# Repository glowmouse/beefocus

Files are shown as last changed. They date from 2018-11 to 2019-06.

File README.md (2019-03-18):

Beefocus
========

Beefocus is an Open Source Hardware/ Software Telescope Focuser 
The goal of the project is to create a high quality DIY focuser that's
relatively easy to build and modify.

It's similar in spirit to other open source focuser projects.  For
example...

- https://sourceforge.net/projects/arduinoascomfocuserpro2diy/
- http://www.scopefocus.info/arduino-focuser-2
- https://sourceforge.net/projects/arduinomoonlitefocuserclone/?source=directory
- https://github.com/aruangra/PnP-Focus

Why start a new project?
------------------------

- **Originally, I needed a custom focuser solution for my telescope**.
  I have a Celestron C11 with a Hyperstar.  When I started this I
  couldn't find a good out of the box solution.
- **I want to try using an ESP-8266 internet of things micro-controller 
  instead of a traditional arduino**.  I've found that every wire you 
  get rid of simplifies your telescope setup and observing
- **I want to open-source the hardware design under a permissive license.**   
  I'm intrigued by the idea of open-source hardware.  I'm including the
  Eagle CAD files for the hardware under a Creative Commons 4.0 license.
  The goal is to make builds as inexpensive and easy as possible.
- This project is a good personal learning experience.

Code Documentation
------------------

Documentation can be found at https://glowmouse.github.io/beefocus/ 

Status March 2019
-----------------

- I have a physical prototype. It's been field tested and
  it worked almost flawlessly.  The issues that I want to fix before
  "Version 1.0" are tracked on the [Github Project Issues Page].
- The [Prototype ESP8266 Firmware] is posted.  The only thing I want to
  fix in the Firmware is the way you hook up to the Wifi Network.
  Right now you have to modify the Firmware Source Code to add your
  SSID and Password.
- I've published a [Prototype Board Design].  I made my prototype using 
  a CNC circuit router. I had an initial version of the board professionally
  fabricated, and it had a flaw :(.  I'll make a new version of the board
  when I make setting the SSID and Password more user friendly.  I'm also
  waiting for some parts from Ebay.
- There is an INDI Driver for Beefocus, the driver is in the
  [INDI Github Repository] in the [3rd Party Beefocus] directory.
- I've created a [Beefocus INDI Usage] page.

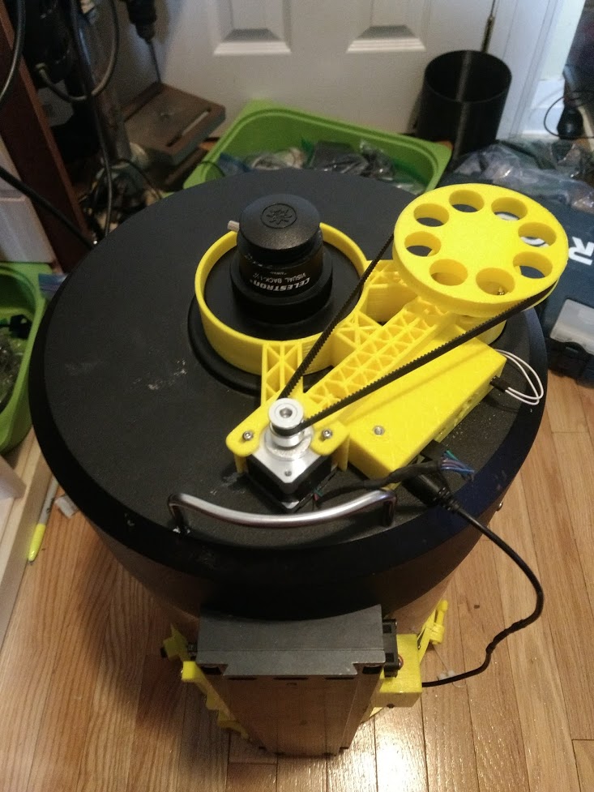
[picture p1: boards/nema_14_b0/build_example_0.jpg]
Nema 14 Build Example


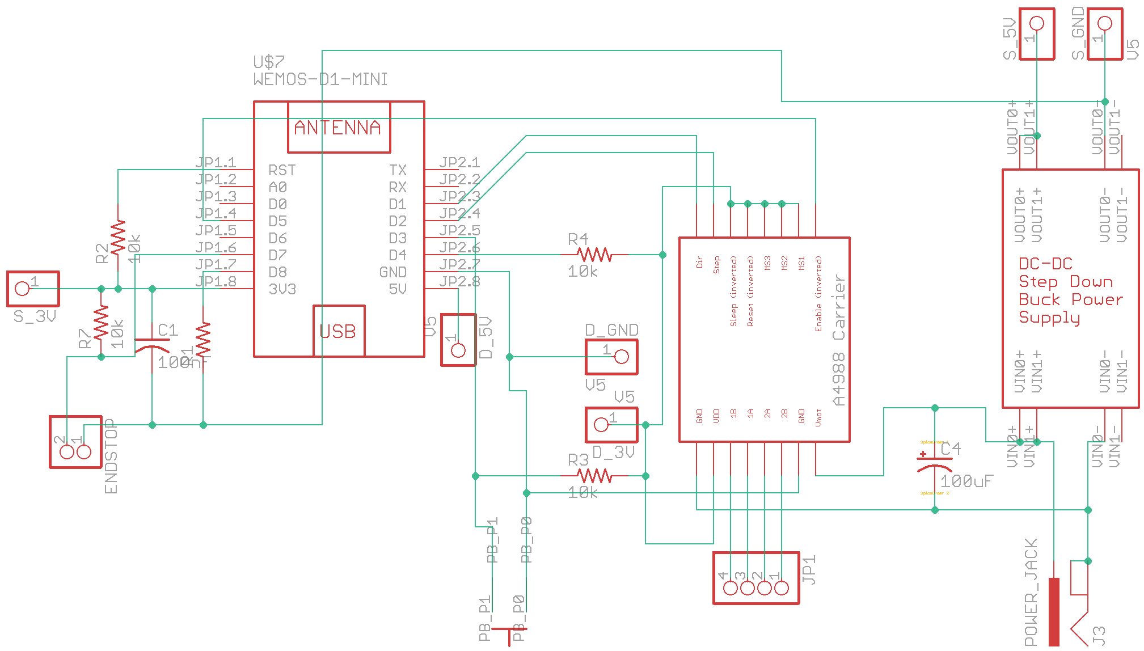
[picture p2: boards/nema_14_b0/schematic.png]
Nema 14 Build Schematic


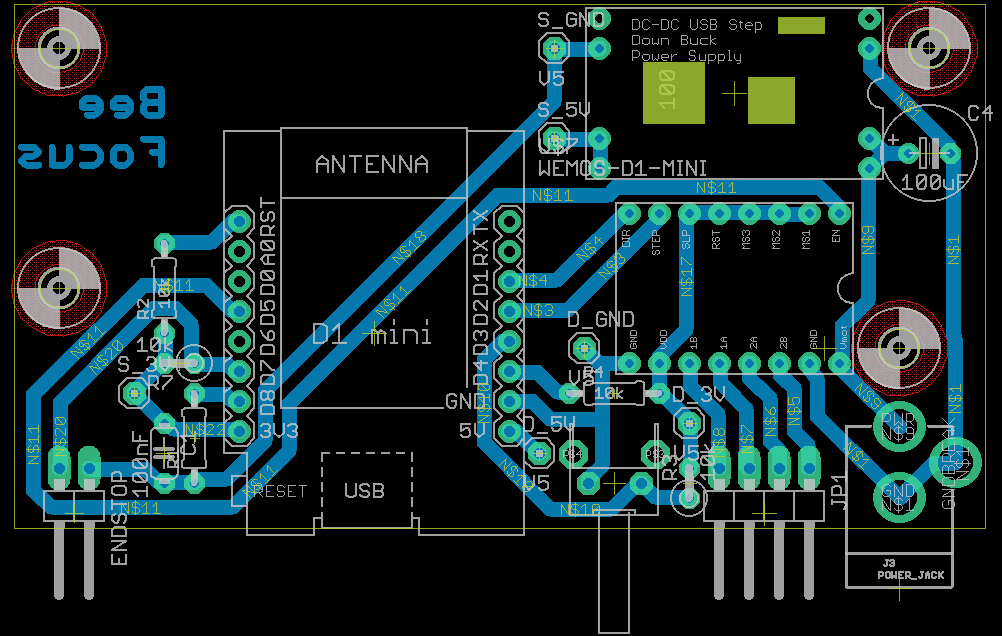
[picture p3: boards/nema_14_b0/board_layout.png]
Nema 14 Build Board


[Github Project Issues Page]:https://github.com/glowmouse/beefocus/issues
[Prototype ESP8266 firmware]: https://github.com/glowmouse/beefocus/tree/master/firmware
[INDI Github Repository]: https://github.com/indilib/indi
[3rd Party Beefocus]: https://github.com/indilib/indi/tree/master/3rdparty/indi-beefocus 
[Prototype board design]: https://github.com/glowmouse/beefocus/tree/master/boards/nema_14_b0
[Beefocus INDI Usage]: https://github.com/glowmouse/beefocus/blob/master/indi_docs/indi_usage_docs.md

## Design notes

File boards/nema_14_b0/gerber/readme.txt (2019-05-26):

Tested gerber files for the nema_14_b0 board.  The board worked, but the DC to DC converters I used in this board aren't sold anymore.  I've moved on to nema_14_b1.

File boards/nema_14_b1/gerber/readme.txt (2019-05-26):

Untested gerber files for the nema_14_b1 board.  I've sent the board out
to get it made, but there are no guarantees that these files will work.

Status:  May 26 2019,  waiting to receive boards.

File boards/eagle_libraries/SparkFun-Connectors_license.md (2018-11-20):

SparkFun Connectors

Licensing: Creative Commons ShareAlike 4.0 International - https://creativecommons.org/licenses/by-sa/4.0/ 

Original source and attriubutio: https://github.com/sparkfun/SparkFun-Eagle-Libraries

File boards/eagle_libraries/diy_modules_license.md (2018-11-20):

DIY Modules Library for EAGLE PCB Design Software has been released under the Creative Commons Attribution 4.0 International License: http://creativecommons.org/licenses/by/4.0.

The library was originally sourced from https://www.diymodules.org/eagle.  The version used by this project is 1.8.0

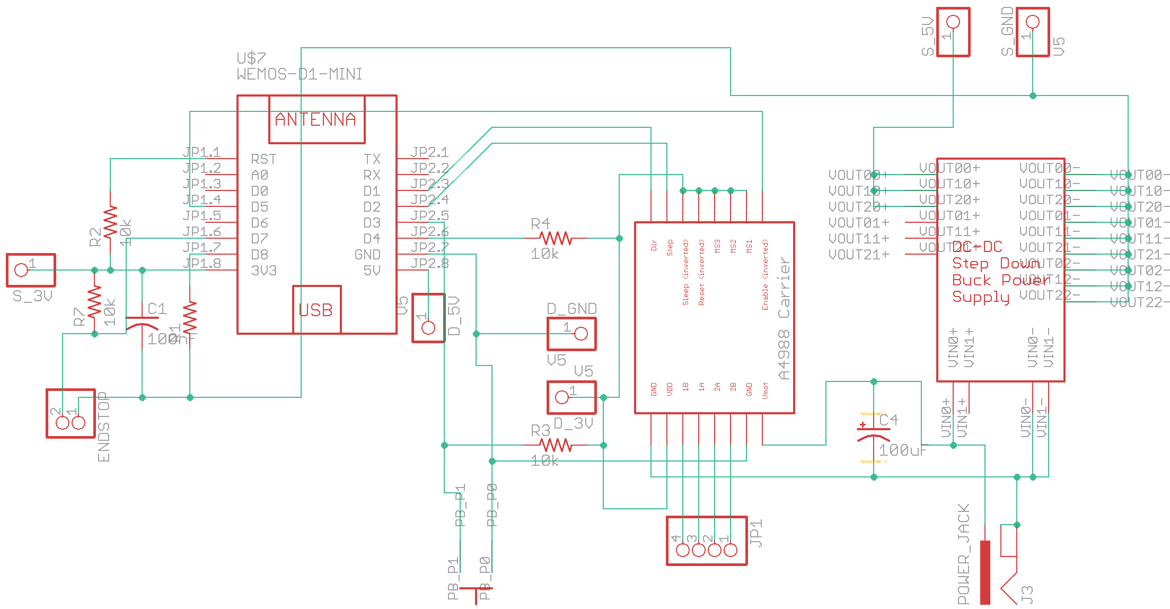
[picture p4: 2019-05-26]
boards/nema_14_b1/schematic.png

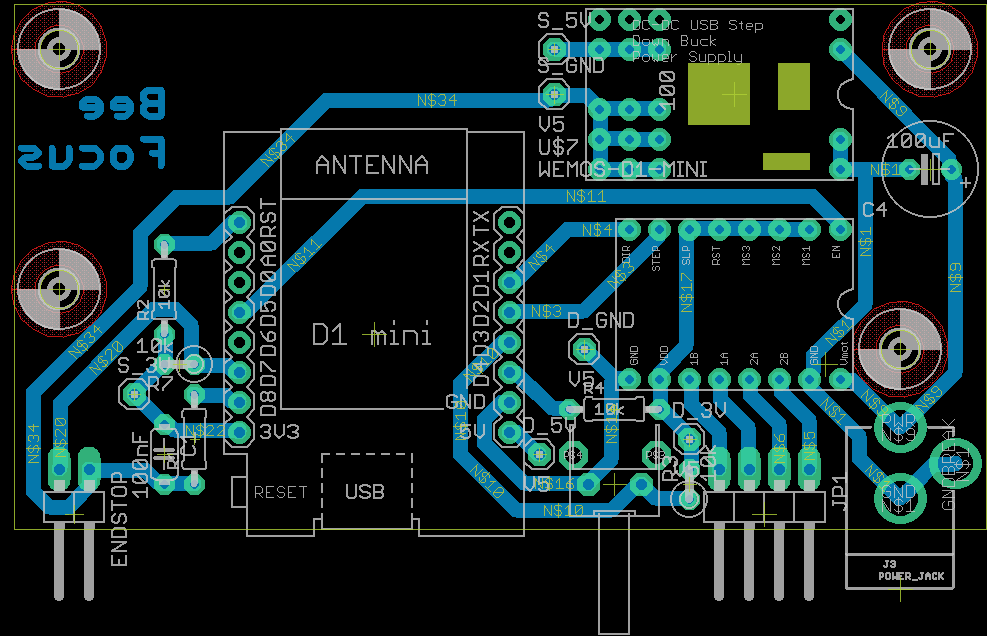
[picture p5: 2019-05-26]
boards/nema_14_b1/board_layout.png

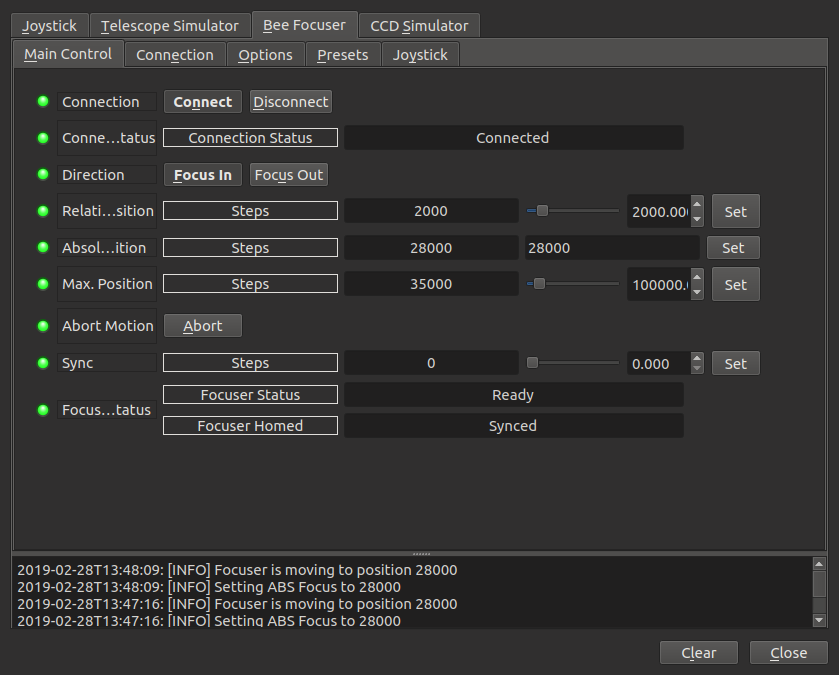
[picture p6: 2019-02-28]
indi_docs/con_sim_abs_dst_ready.png

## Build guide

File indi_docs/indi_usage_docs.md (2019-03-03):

Beefocused
==========

Beefocused is an Open Source Hardware/ Software Telescope Focuser
The goal of the project is to create a high quality DIY focuser that's
relatively easy to build and modify.

Installation
------------

- Beefocused can only be built from source right now (and only on Indi -
  https://indilib.org/ ) - ASCOM drivers haven't been written yet.  
  If you're interested in building one send an email to 
  andrew.brownbill@gmail.com

Features
--------

- Beefocused talks to the INDI computer using WiFi.  This is nice because
  it means there's one less wire on the telescope to worry about.  It does 
  mean that the telescope needs a WiFi hotspot,  but that's becoming more 
  common now that people are running telescopes from compute sticks and 
  Raspberry Pis that are mounted directly onto the scope.
- The default built uses a Nema 14 Stepper motor for positioning - these motors
  are widely used by 3D printers.  The Motor's step rate is 1.8 degrees 
  (200 steps / rotation), so it's reasonably accurate.
- The electronic parts for a Beefocused will cost you about $25 on eBay.
  That includes the Nema 14 Stepper Motor. 
- Beefocus focusers operate as either Absolute or Relative focusers,
  depending on the build.  The focuser supports either automatic homing at
  start up or manual syncing.

Using the Simulated Focuser
---------------------------

The Beefocused Indi driver has a "Simulation" mode that's very close to what
you'll see if you use the actual hardware.  Simulation mode is selected by
going to the BeeFocused connection tab and selecting a Simulated connection

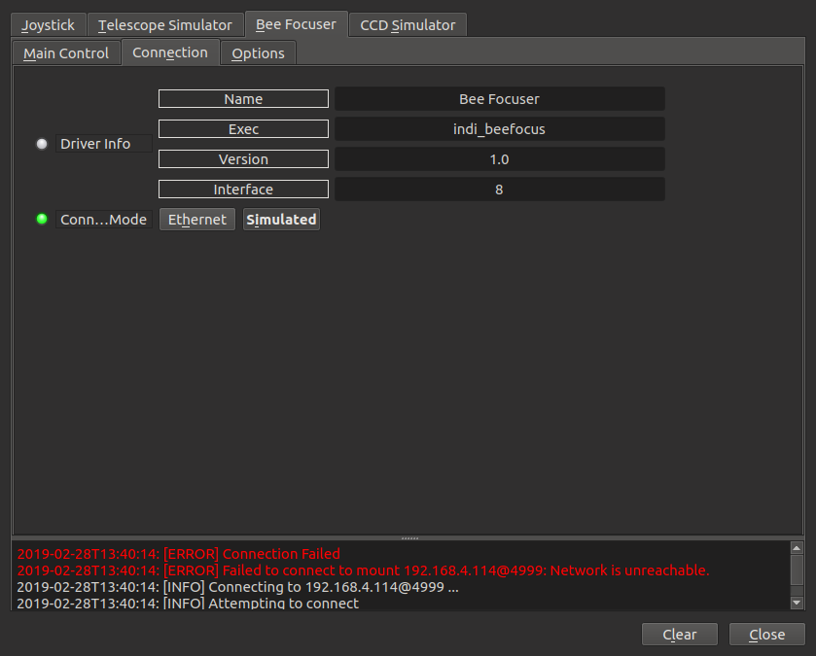
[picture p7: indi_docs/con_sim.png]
Selecting a Simulated Connection


You'll need to go to the Main focuser menu and "connect" to the Simulated
Focuser, the way you'd connect to an actual focuser.

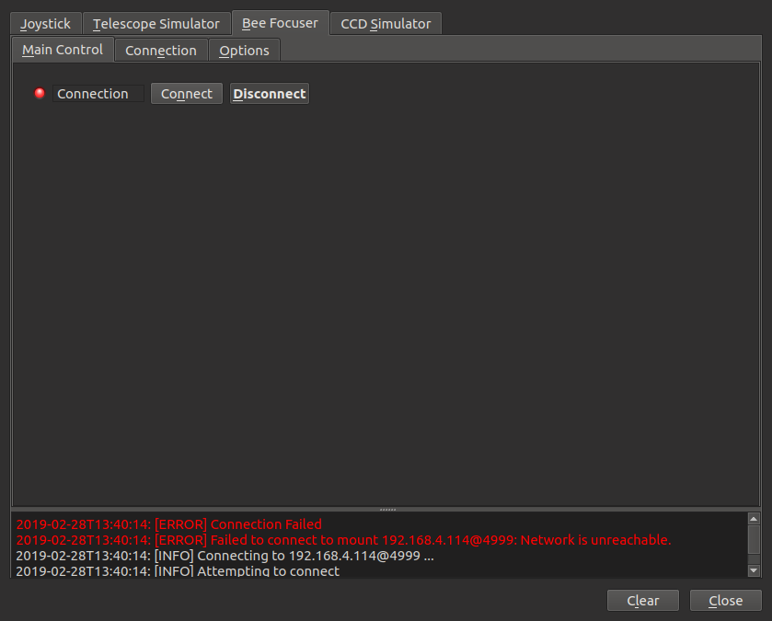
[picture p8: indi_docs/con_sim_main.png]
Simulated Focuser Connection Menu


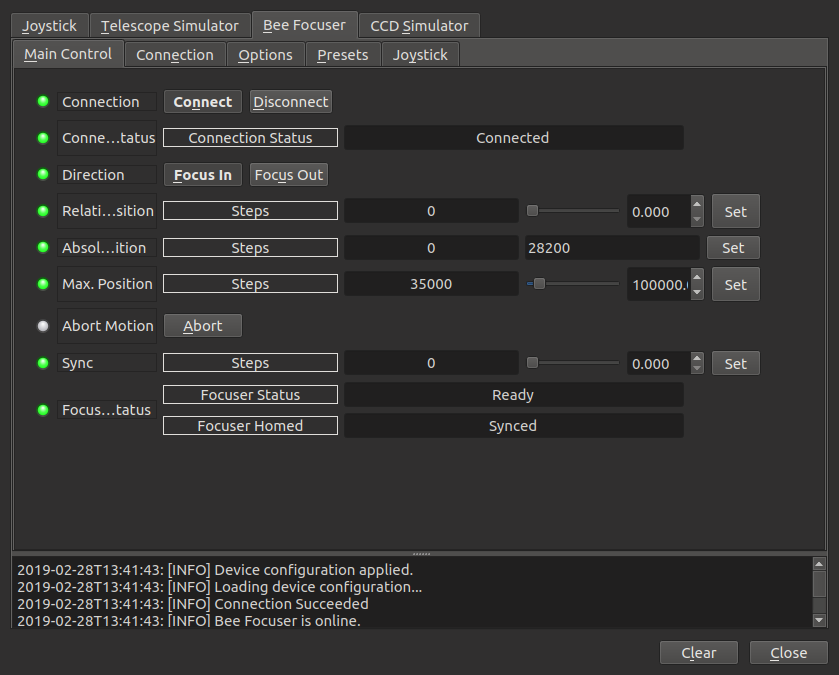
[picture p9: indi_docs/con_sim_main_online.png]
Simulated Focuser Online


You can start moving the simulated focuser by pressing the Absolute Position
Set Button.  The Focuser Status message box will change from Ready to Moving,
and the Absolute Position of the focuser will begin changing.

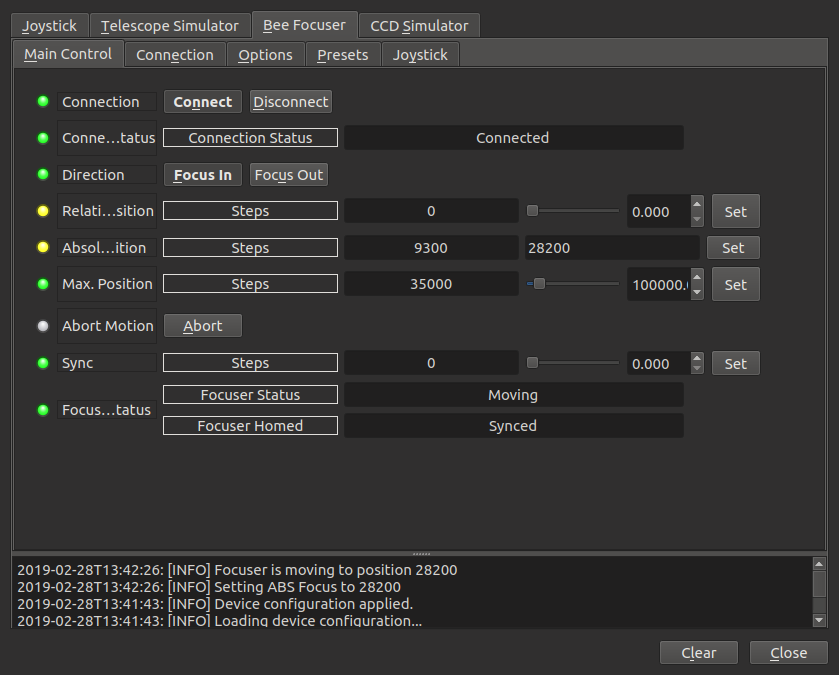
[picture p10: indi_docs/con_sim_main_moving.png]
Simulated Focuser Moving


A move can be interrupted by pressing the Abort button.  If you try to move
the focuser past the Maximum Position the driver will generate an Error
message

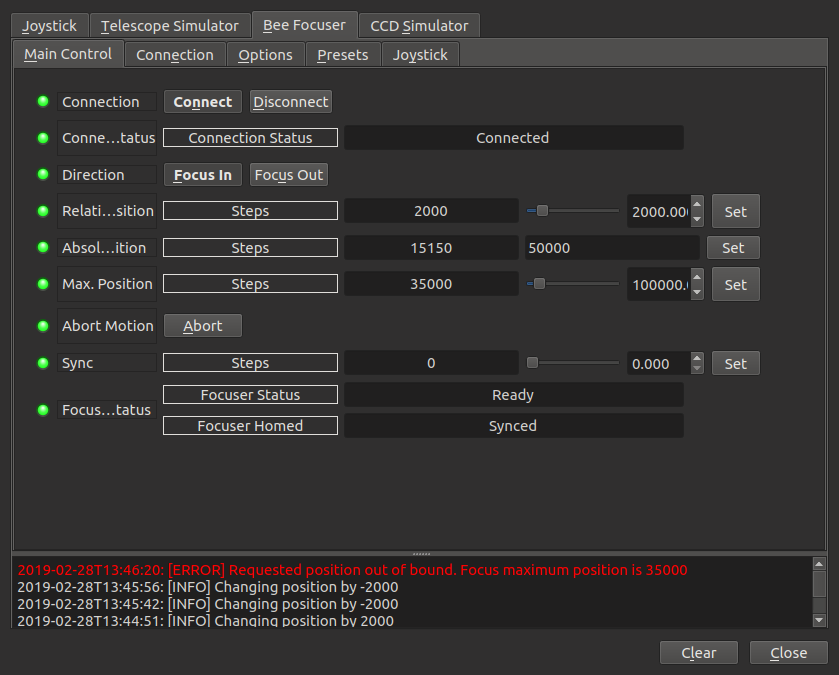
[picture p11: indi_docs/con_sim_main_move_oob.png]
Out of bounds error message


If the focuser's hardware supports a home switch the focuser will 
automatically move to it's home, or zero position, the first time INDI 
connects.  The sync switch can also be used to set the Focuser's current
absolute position.  In this example the Sync switch is used to reset the
absolute position to 2000.
 
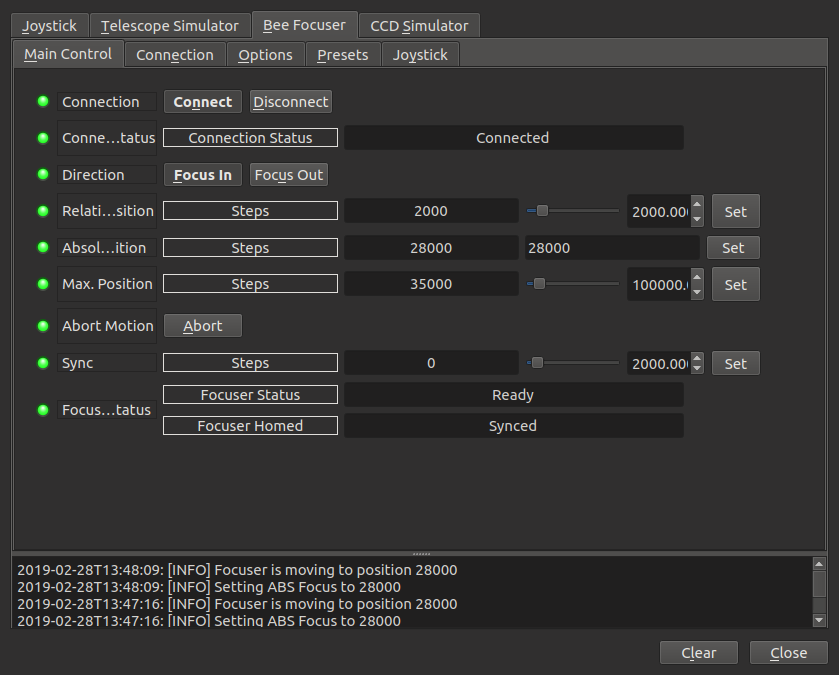
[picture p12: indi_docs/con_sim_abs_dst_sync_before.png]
Sync Before

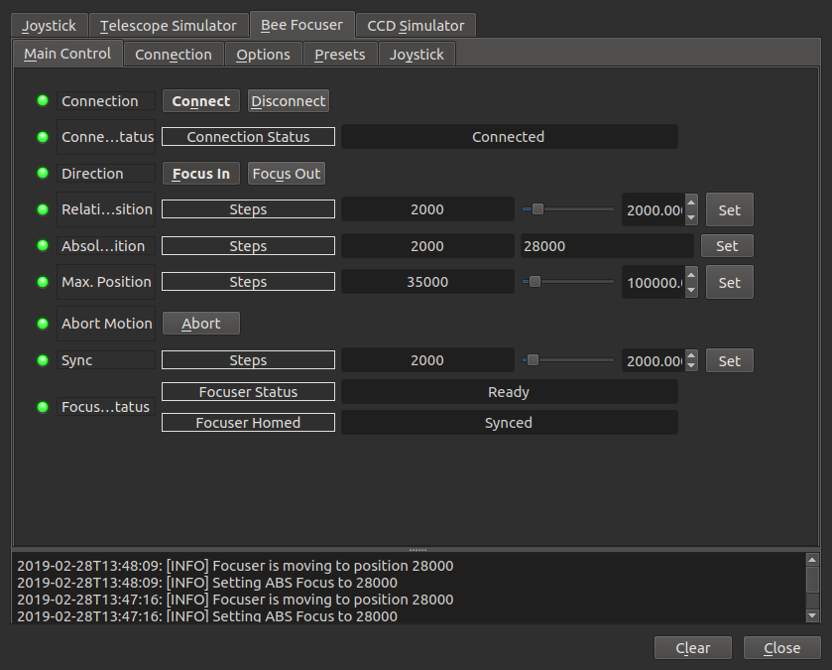
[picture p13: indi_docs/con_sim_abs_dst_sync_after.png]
Sync After


The focuser can move relative to it's current position.  In this mode the
user changes the Relative Position field number to the number of positions they
want the focuser to move (2000 in this example) and presses set.  Pressing
Set again will cause the focuser to move again.

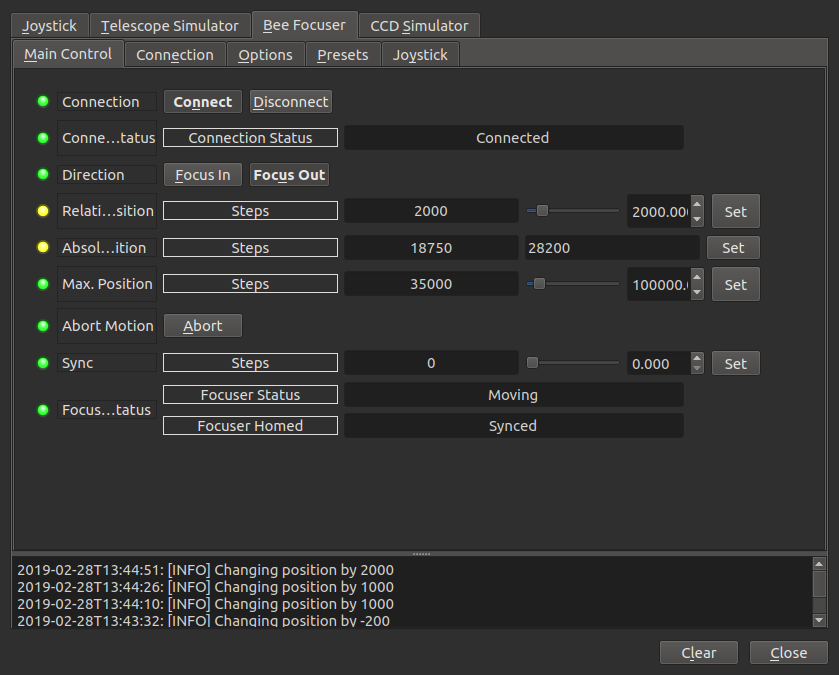
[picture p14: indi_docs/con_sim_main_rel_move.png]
Relative Move +2000


The Focus In and Focus Out buttons control the direction of relative movements.
In the last example the Focus Out switch was active. In the example the 
Focus In switch was active and then the Relative Position Set button was 
pressed twice.  The Focuser moved by -2000 each time.

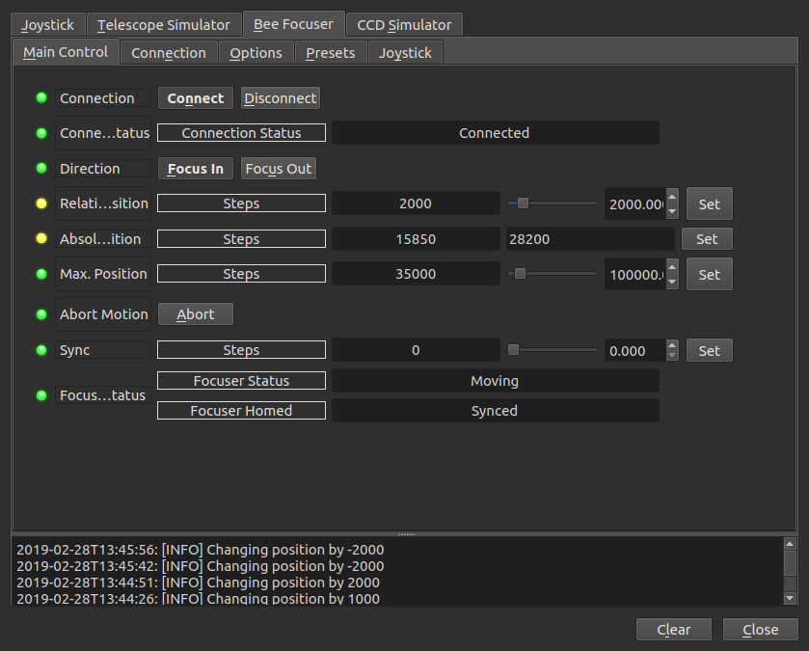
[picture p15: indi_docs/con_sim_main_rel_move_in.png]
Relative Move -2000

 
A game controller is a convenient way to manually operate the focuser.  To use
the game controller, set a relative focuser movement rate that works for 
setup (100 was good for me),  turn on Joystick in the Options Tab

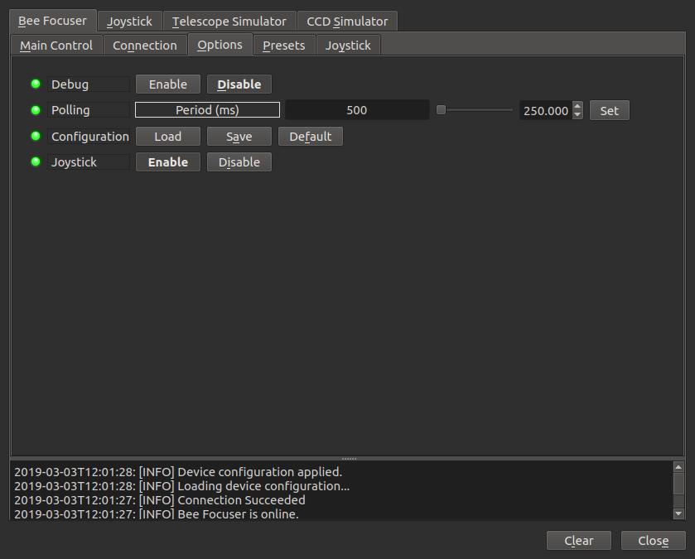
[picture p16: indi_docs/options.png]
options


And set-up the Joystick Buttons in the Joystick TAB.  I used the bottom
buttons on my game controller to focus in and out (BUTTON_7 and BUTTON_8),
and the "A" button to Abort (BUTTON_2).

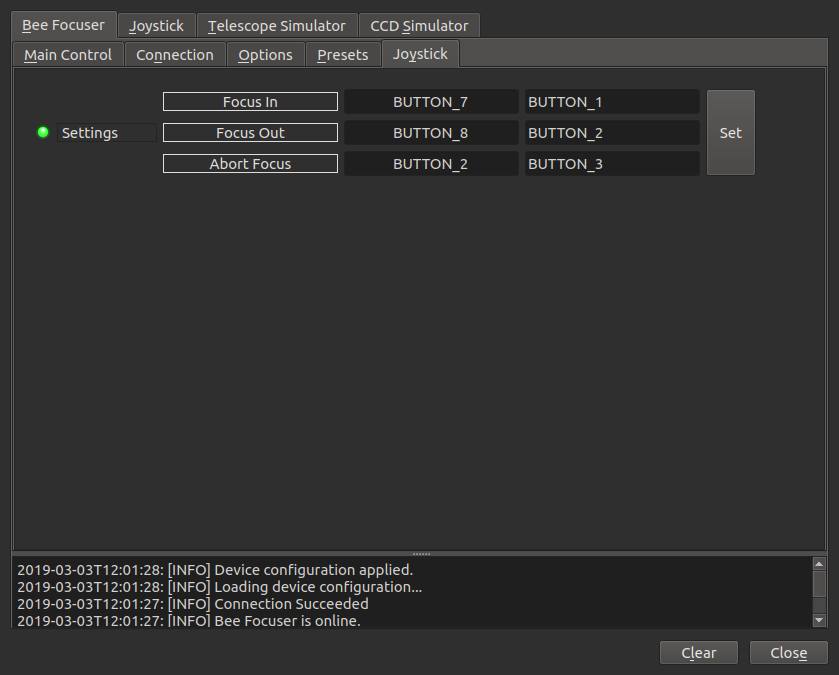
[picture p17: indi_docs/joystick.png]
joystick


I know that absolute position 28000 is close to my telescope's focal point, 
so I've added a 28000 entry to the Presets tab. 

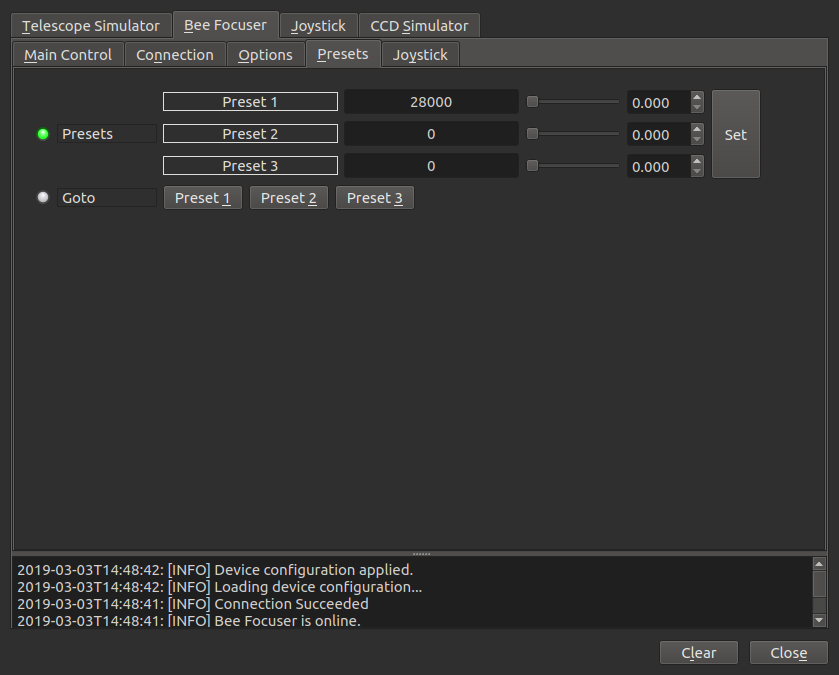
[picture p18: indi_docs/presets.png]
Presets


To connect to the actual focuser, switch the connection type to ethernet and
enter the address of the focuser.  The port is always 4999.  

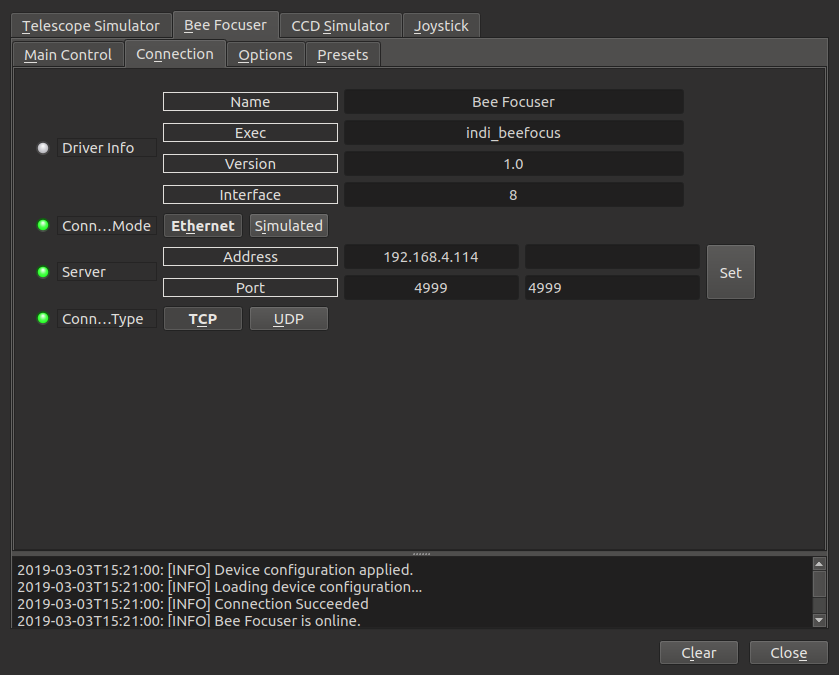
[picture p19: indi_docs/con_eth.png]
Ethernet Connection


The main control tab of the actual focuser and simulated focuser are the same.

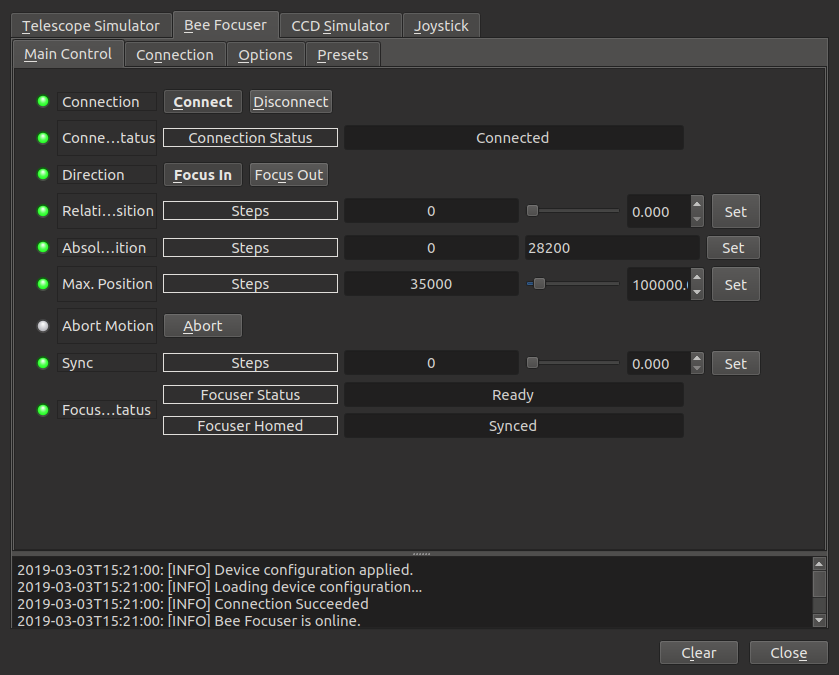
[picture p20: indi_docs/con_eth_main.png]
Ethernet Main Tab


Installing Firmware 
-------------------

TODO

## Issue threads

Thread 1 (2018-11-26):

External nema_14_b0 board manufacture and process documentation

glowmouse, 2018-11-26:
- Document steps to have an inexpensive nema_14_b0 board made
- Post files
- Acceptance:  working board

glowmouse, 2019-03-17:
Got the board back.  The board had a flaw that wasn't in the prototype because I had to re-do the board to make sure all of the libraries I used were properly licensed.  I want to replace one of the jumpers in my current board design with a switch to make it more user friendly.  The switch will be used to soft reboot the board when you want to reprogram an SSID and/or password.

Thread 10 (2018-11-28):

Firmware should remember that it's homed - driver should check for home state

glowmouse, 2018-11-28:
When the current current INDI driver starts it issues a HOME command to the focuser.  If the focuser is already homed (say we have to shutdown and re-init INDI) then the observer has to wait for the stepper motor to wind back to home, and wind back to focus.

- Add a Home flag to the focuser's firmware status
- Add a command to output the focuser's home status.  i.e., HOMESTATUS
- Have the driver check to see if the focuser is alread homed before beginning
- Maybe add a re-home button to the driver's interface.

Closed 2018-12-22.

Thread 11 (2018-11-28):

Implement and Verify power saving "sleep" mode

glowmouse, 2018-11-28:
The focuser sleep mode currently turns off the stepper motor to save power.  It looks like the ESP8266 power consumption is still around 100ma.  so maybe .5 watts @ 5V.  That's a lot of you're running off a battery.

I should look for ways to reduce power on the ESP8266.  This may be a good start point:

https://openhomeautomation.net/esp8266-battery

glowmouse, 2018-12-23:
Power draw with the stepper engaged was about 200ma at 12V.
Power draw in "sleep mode" was about 20ma at 12V.

Closed 2018-12-23.

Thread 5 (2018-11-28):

CommandParser::Deltas should only allow one state change

glowmouse, 2018-11-28:
All of the current commands are lines of text with one of the following syntaxes:

keyword
keyword integer

for example

home
abs_pos 1000
sleep
awaken

check_for_commands would be cleaner if it returned a token for the first word and an optional integer argument.  i.e.

typedef enum  {
   E_ABS_POS,
   E_HOME,
   ...
} Token;

struct {
   Token command;
   int optional_argument;
}

glowmouse, 2018-12-09:
Resolved in https://github.com/glowmouse/beefocus/commit/8efc33bf5270e593503e3c90f5f6f3b546b9e07d

Closed 2018-12-09.

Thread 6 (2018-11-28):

Pin Specifics should be in the hardware interface

glowmouse, 2018-11-28:
FocuserState currently defines 4 pins:

dirPin - Output:  Stepper motor direction pin
stepPin - Output:  The pin that moves the motor 1 step
enaPin - Output:  The pin that enables the stepper motor
homePin - Input:  1 when the home switch is on

The problem is that these values are specific to the ESP8266 Nema 14 board.  Pin values are specific to a particular board.  Replacing the defines with an enum and then doing the mapping in the board interface would be cleaner.  HardwareInterface would accept pins in terms of the enum.

Maybe also add a build argument to the HardwareESP8266 constructor, so if a new ESP8266 board is made we can easily change the device agnostic -> build pin mapping.

glowmouse, 2018-12-08:
The focuser state is hardware agnostic.  I'll file a new ticket for the build argument if I decide to do that later.

Closed 2018-12-08.

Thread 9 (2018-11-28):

Indi Prototype Driver moved to 3rd party

glowmouse, 2018-11-28:
The current prototype driver on

https://github.com/glowmouse/indi

is implemented in https://github.com/glowmouse/indi/tree/master/libindi/drivers/focuser

If the firmware is used as a simulator (which would be arguably elegant) then we probably want to put the driver somewhere in 3rd_party instead.

Closed 2019-03-17.

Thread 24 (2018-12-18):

Focuser should gracefully handle interruptions while moving or homing

glowmouse, 2018-12-18:
The original firmware would enter an error state if you issued it an command while homing or moving.  The 1.0 firmware should gracefully handle interruptions.

Closed 2018-12-22.

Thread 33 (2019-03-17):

Firmware needs to have a friendly way to set an SSID and Password

glowmouse, 2019-03-17:
Right now the Wifi Password and SSID are set by modifying Wifi Secrets.  Other ESP8266 projects have brought up a web page and recorded the information in the ESP8266 flash.  That seems like a much more friendly way to go.

This probably means that the focuser will need a user accessible soft reset switch.  In the original board design I exposed a 2 pin dupont connector for flashing the firmware.  In practice I found that I didn't have to close the wires on the connector to flash, the pull-up resistors seem to have done their job.  I think I'll use that connector to trigger a soft reset that will allow users to reset their SSID and Password.

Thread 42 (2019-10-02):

add feature

dragonlost, 2019-10-02:
Hello.
Your project is very interesting. I would like to know if you have planned to add the following functionality:

Possibility to connect 2 buttons and 1 screen (via i2c) to have a remote control for manual use (requires 4 wires).

The ability to program a backslash via the indi driver (just add on indi base focuser)

The ability to connect to an existing network with wemos via a web page.

The ability to communicate via usb.

glowmouse, 2019-10-05:
Thanks for the feedback.  I'm planning to work on the project more this winter (I live in Toronto, Canada).  One of the things I thought about this summer was how to get the project to a state where other people can use it.  My thoughts were:

- I think I need to create an interface that will let you set your Wifi SSID and Password.  Right now you just program it into the firmware.  My thought was to have the ESP8266 create a default hotspot with a web page and let you setup your configuration information there.  You can see the start in the wifi_html directory (configuration.html).
- I need to get more feedback on what other people need in a focuser, or get other people to try it out.  Right now I'm using a C11 and a hyperstar, which is a niche setup.  I really appreciate your comments.
- I'm the only person I know (locally) that uses Linux to run a telescope.  i.e., an ascom driver would be good.

_Possibility to connect 2 buttons and 1 screen (via i2c) to have a remote control for manual use (requires 4 wires)._

In one of my board designs I thought about using the analog input on the ESP8266 to get button input.  I backed off the idea because it didn't fit into my physical build.  I didn't push on it because I had the idea that I could use a wireless game controller (i.e., the INDI joystick interface) to get the same effect.

Would you be able to talk about use cases where you think this would be valuable?  All of my 'in the field' experience is with a telescope setup that's "camera only", and almost completely automated.

_The ability to program a backslash via the indi driver (just add on indi base focuser)_

I agree.  I thought that this could be part of the configuration on the actual focuser.  i.e., when you're setting up an SSID and Password you can also add settings like backlash.  It seems like a setting that's bound to your physical setup and unlikely to change often.

_The ability to connect to an existing network with wemos via a web page._

Like a configuration page (i.e., what I mentioned above), or a web page that would let you operate the focuser directly?  Both seem like good ideas.

_The ability to communicate via usb._

I agree that this would expand the potential audience, and it's doable.  It's a matter of prioritisation.

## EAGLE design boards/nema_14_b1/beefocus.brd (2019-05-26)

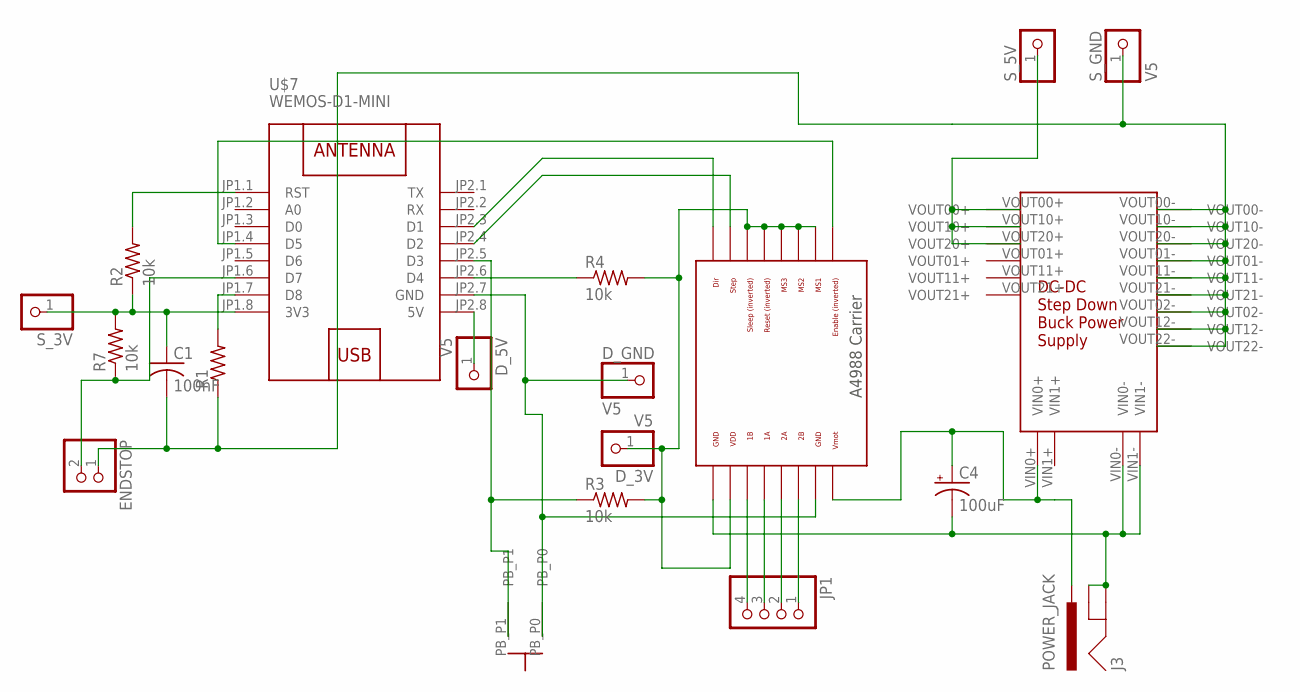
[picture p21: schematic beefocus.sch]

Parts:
C1: 100nF; C050-024X044
C4: 100uF; E3,5-8
D_3V, D_5V: V5; 1X01
D_GND: V5; 1X01
ENDSTOP: PINHD-1X2/90; 1X02/90
J3: POWER_JACK; POWER_JACK_PTH
JP1: PINHD-1X4/90; 1X04/90
R1: R-US_0204/7; 0204/7
R2, R4: 10k; 0204/7
R3, R7: 10k; 0309V
S_3V, S_5V: PINHD-1X1; 1X01
S_GND: V5; 1X01
U$1: POLOLU_A4983CARRIER; A4988BREAKOUT
U$6: DCPOWERCONV_R2
U$7: WEMOS-D1-MINI
U$8: BUTTON6X6X10MMSIDE

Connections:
unnamed: C4.-, J3.GND, J3.GNDBREAK, U$1.GND@0 (GND), U$6.VIN0-, U$6.VIN1-
unnamed: D_5V.1, U$7.JP2.8 (5V)
unnamed: U$1.STEP, U$7.JP2.4 (D2)
unnamed: U$1.DIR, U$7.JP2.3 (D1)
unnamed: JP1.1, U$1.2B
unnamed: JP1.2, U$1.2A
unnamed: JP1.3, U$1.1A
unnamed: JP1.4, U$1.1B
unnamed: C4.+, J3.PWR, U$1.VMOT, U$6.VIN0+
unnamed: R3.1, U$7.JP2.5 (D3), U$8.PB_P1
unnamed: U$1.EN, U$7.JP1.4 (D5)
unnamed: R2.2, U$7.JP1.1 (RST)
unnamed: R1.2, U$7.JP1.7 (D8)
unnamed: D_GND.1, U$1.GND, U$7.JP2.7 (GND), U$8.PB_P0
unnamed: D_3V.1, R3.2, R4.2, U$1.MS1, U$1.MS2, U$1.MS3, U$1.RST, U$1.SLP (SLEEP), U$1.VDD
unnamed: ENDSTOP.2, R7.1, U$7.JP1.6 (D7)
unnamed: C1.1, R2.1, R7.2, S_3V.1, U$7.JP1.8 (3V3)
unnamed: R4.1, U$7.JP2.6 (D4)
unnamed: C1.2, ENDSTOP.1, R1.1, S_GND.1, U$6.VOUT00-, U$6.VOUT01-, U$6.VOUT02-, U$6.VOUT10-, U$6.VOUT11-, U$6.VOUT12-, U$6.VOUT20-, U$6.VOUT21-, U$6.VOUT22-
unnamed: S_5V.1, U$6.VOUT00+, U$6.VOUT10+, U$6.VOUT20+

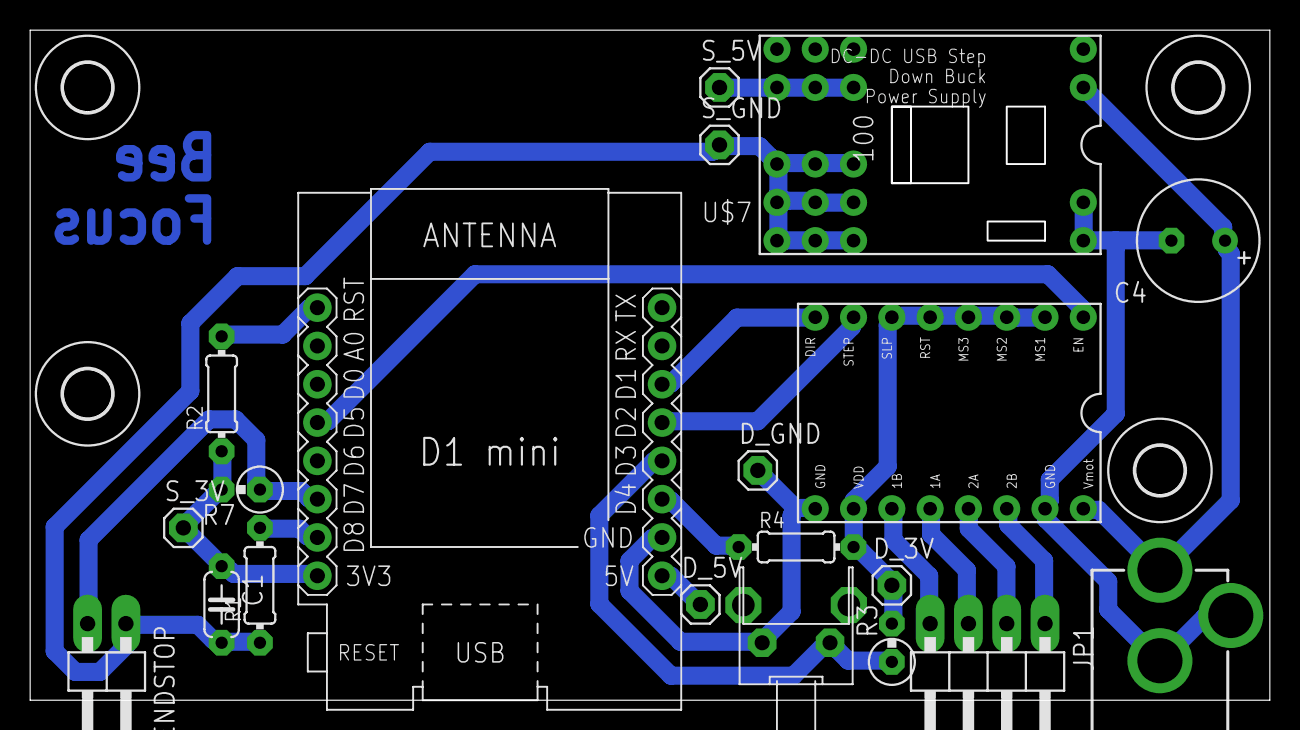
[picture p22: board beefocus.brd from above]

Board: 2 copper layers, 82.2 x 44.4 mm, 24 parts (0 on the bottom side), 20 nets.

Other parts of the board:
U$2, U$3, U$4, U$5: 3,2

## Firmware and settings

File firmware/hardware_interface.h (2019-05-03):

#ifndef __HARDWARE_INTERFACE_H__
#define __HARDWARE_INTERFACE_H__

#include <unordered_map>
#include <string>
#include "basic_types.h"

struct EnumHash
{
  // @brief Type convert any enum type to a size_t for hashing
  template <class T>
  std::size_t operator()(T enum_val) const
  {
    return static_cast<std::size_t>(enum_val);
  }
};

class HWI
{
  public:

  virtual ~HWI() {}

  enum class Pin {
    START_OF_PINS = 0,
    STEP = 0,
    DIR,
    MOTOR_ENA,
    HOME,
    END_OF_PINS 
  };

  enum class PinState {
    START_OF_PIN_STATES = 0,
    STEP_ACTIVE = 0,
    STEP_INACTIVE,
    DIR_FORWARD,
    DIR_BACKWARD,
    MOTOR_ON,       // 0 on the nema build
    MOTOR_OFF,      // 1 on the nema build
    HOME_ACTIVE,    // 0 on the nema build
    HOME_INACTIVE,  // 1 on the nema build
    END_OF_PIN_STATES
  };

  // Arduino.h uses #define to redefine OUTPUT and INPUT,  so use
  //           M_OUTPUT and M_INPUT here.  Thanks Obama.
  enum class PinIOMode {
    START_OF_PIN_IO_MODES = 0,
    M_OUTPUT = 0,
    M_INPUT = 1,
    END_OF_IO_MODES
  };

  const static std::unordered_map<Pin,std::string,EnumHash> pinNames;
  const static std::unordered_map<PinState,std::string,EnumHash> pinStateNames;
  const static std::unordered_map<PinIOMode,std::string,EnumHash> pinIOModeNames;

  virtual void DigitalWrite( Pin pin, PinState state ) = 0;
  virtual void PinMode( Pin pin, PinIOMode mode ) = 0;
  virtual PinState DigitalRead( Pin pin) = 0;
};

// @brief Increment operator for Hardware Interface Pin
//
// @param[in] pin - The pin to increment. 
// @return - The next value in the Enum.
//
inline HWI::Pin& operator++( HWI::Pin &pin ) 
{
  return BeeFocus::advance< HWI::Pin, HWI::Pin::END_OF_PINS >( pin );
}

// @brief Increment operator for Hardware Interface Pin State
//
// @param[in] pinState - The pin state to increment. 
// @return - The next value in the Enum.
// 
inline HWI::PinState& operator++( HWI::PinState &pin ) 
{
  return BeeFocus::advance< HWI::PinState, HWI::PinState::END_OF_PIN_STATES >( pin );
}

// @brief Increment operator for Hardware Interface Pin IO Mode
//
// @param[in] pinIoMode - The pin IO Mode to increment. 
// @return - The next value in the Enum.
// 
inline HWI::PinIOMode& operator++( HWI::PinIOMode &pin ) 
{
  return BeeFocus::advance< HWI::PinIOMode, HWI::PinIOMode::END_OF_IO_MODES >( pin );
}

#endif

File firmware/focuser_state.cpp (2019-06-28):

#include <iterator>
#include <vector>
#include <string>
#include <memory>
#include "command_parser.h"
#include "wifi_debug_ostream.h"
#include "focuser_state.h"

using namespace FS;

//
// Implementation of the Focuser class
//
// As described in focuser_state.h, the Focuser Class has two main jobs:
//
// 1. It accepts new commands from a network interface
// 2. Over time, it manipulates a hardware interface to implement the commands
//
// At construction time the Focuser is provided three interfaces - an
// interface to the network (i.e., a Wifi Connection), an interface to the 
// the hardware (i.e., the pins in a Micro-Controller) an interface for
// debug logging, and the focuser's hardware parameters
//
// Once the focuser is initialized, the loop function is used to real time
// updates.  The loop function returns a minimum time that the caller should
// wait before calling loop again, in microseconds.
//
// Private member functions prefaced with 'do' are command processors.  They
// take input for a command that came from the focuser's network interface
// and adjust the Focuser class's state so it can process that input. For
// example, the doHome method pushes a State::STOP_AT_HOME command onto the
// focuser's state stack.
//
// When loop is called, the Focuser class processess the top command on its
// state stack.  The methods that do this processing are prefaced with 
// 'state'.  For example, stateStopAtHome checks to see if the hardware
// interface's home pin is active.  If it is, it pops it's current state
// (State::STOP_AT_HOME' from the focuser's state stack and considers the
// operating finished.  If it isn't, it pushes commands onto the focuser's
// state stack that will result in the focuser rewinding one step.
//

/////////////////////////////////////////////////////////////////////////
//
// Public Interfaces
//
/////////////////////////////////////////////////////////////////////////

Focuser::Focuser(
    std::unique_ptr<NetInterface> netArg,
    std::unique_ptr<HWI> hardwareArg,
    std::unique_ptr<DebugInterface> debugArg,
    const BuildParams params
) : buildParams{ params }
{
  focuserPosition = 0;
  isSynched = false;
  time = 0;
  uSecRemainder = 0;
  timeLastInterruptingCommandOccured = 0;
  motorState = MotorState::OFF;

  std::swap( net, netArg );
  std::swap( hardware, hardwareArg );
  std::swap( debugLog, debugArg );
  
  DebugInterface& dlog = *debugLog;
  dlog << "Bringing up net interface\n";
  
  // Bring up the interface to the controlling computer

  net->setup( dlog );
  WifiDebugOstream log( debugLog.get(), net.get() );

  //
  // Set the pin modes 
  //
  hardware->PinMode(HWI::Pin::STEP,       HWI::PinIOMode::M_OUTPUT );  
  hardware->PinMode(HWI::Pin::DIR,        HWI::PinIOMode::M_OUTPUT );  
  hardware->PinMode(HWI::Pin::MOTOR_ENA,  HWI::PinIOMode::M_OUTPUT );  
  hardware->PinMode(HWI::Pin::HOME,       HWI::PinIOMode::M_INPUT ); 
 
  //
  // Set the output pin defaults and internal state
  // 
  setMotor( log, MotorState::ON ); 

  dir = Dir::FORWARD;
  hardware->DigitalWrite( HWI::Pin::DIR, HWI::PinState::DIR_FORWARD); 
  hardware->DigitalWrite( HWI::Pin::STEP, HWI::PinState::STEP_INACTIVE );

  log << "Focuser is up\n";
}

unsigned int Focuser::loop()
{
  ptrToMember function = stateImpl.at( stateStack.topState() );
  const unsigned uSecToNextCall = (this->*function)();
  uSecRemainder += uSecToNextCall;
  time += uSecRemainder / 1000;
  uSecRemainder = uSecRemainder % 1000;
  net->flush();
  return uSecToNextCall;
}

/////////////////////////////////////////////////////////////////////////
//
// Private Interfaces
//
// Section Overview:
// 
// 1. Constant Data
// 2. Methods that interpret input from the network
// 3. Methods that process the commands over time
// 4. Utility Methods
// 
/////////////////////////////////////////////////////////////////////////


/////////////////////////////////////////////////////////////////////////
//
// Section 1.  Constant Data
//
/////////////////////////////////////////////////////////////////////////

// What does the focuser execute if it's in a particular state?
const std::unordered_map<State,unsigned int (Focuser::*)( void ),EnumHash>
  Focuser::stateImpl =
{
  { State::ACCEPT_COMMANDS,           &Focuser::stateAcceptCommands },
  { State::DO_STEPS,                  &Focuser::stateDoingSteps },
  { State::STEPPER_INACTIVE_AND_WAIT, &Focuser::stateStepInactiveAndWait },
  { State::STEPPER_ACTIVE_AND_WAIT,   &Focuser::stateStepActiveAndWait },
  { State::SET_DIR,                   &Focuser::stateSetDir },
  { State::MOVING,                    &Focuser::stateMoving },
  { State::STOP_AT_HOME,              &Focuser::stateStopAtHome },
  { State::SLEEP,                     &Focuser::stateSleep },
  { State::ERROR_STATE,               &Focuser::stateError }
};

// Bind State Enums to Human Readable Debug Names
const StateToString FS::stateNames =
{
  { State::ACCEPT_COMMANDS,               "ACCEPTING_COMMANDS" },
  { State::DO_STEPS,                      "DO_STEPS"           },
  { State::STEPPER_INACTIVE_AND_WAIT,     "STEPPER_INACTIVE"   },
  { State::STEPPER_ACTIVE_AND_WAIT,       "STEPPER_ACTIVE"     },
  { State::SET_DIR,                       "SET_DIR"            },
  { State::MOVING,                        "MOVING"             },
  { State::STOP_AT_HOME,                  "STOP_AT_HOME"       },
  { State::SLEEP,                         "LOW_POWER"          },
  { State::ERROR_STATE,                   "ERROR ERROR ERROR"  },
};

// Implementation of the commands that the Focuser Supports 
const std::unordered_map<CommandParser::Command,
  void (Focuser::*)( CommandParser::CommandPacket),EnumHash> 
  Focuser::commandImpl = 
{
  { CommandParser::Command::Abort,      &Focuser::doAbort },
  { CommandParser::Command::Home,       &Focuser::doHome },
  { CommandParser::Command::LHome,      &Focuser::doLHome },
  { CommandParser::Command::PStatus,    &Focuser::doPStatus },
  { CommandParser::Command::MStatus,    &Focuser::doMStatus },
  { CommandParser::Command::SStatus,    &Focuser::doSStatus },
  { CommandParser::Command::ABSPos,     &Focuser::doABSPos },
  { CommandParser::Command::RELPos,     &Focuser::doRELPos },
  { CommandParser::Command::Sync,       &Focuser::doSync},
  { CommandParser::Command::Firmware,   &Focuser::doFirmware},
  { CommandParser::Command::Caps,       &Focuser::doCaps},
  { CommandParser::Command::DebugOff,   &Focuser::doDebugOff},
  { CommandParser::Command::NoCommand,  &Focuser::doError },
};
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

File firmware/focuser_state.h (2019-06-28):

#ifndef __FOCUSER_STATE_H__
#define __FOCUSER_STATE_H__

#include <vector>
#include <memory>
#include <string>
#include <assert.h>
#include <unordered_map>
#include "net_interface.h"
#include "hardware_interface.h"
#include "command_parser.h"

#ifdef GTEST_FOUND
#include <gtest/gtest_prod.h>
#endif

///
/// @brief Focuser Namespace
/// 
/// This is a collection of code that has to do with the focuser's
/// state.  The code in this namespace 
///
/// - Initializes the hardware
/// - Moves the stepper motor
/// - Accepts input from the network
///
/// \b Concepts
///
/// - <b> Basic Flow: </b>
///       Callers run the focuser by repeatly calling Focuser::loop; this 
///       is simular to the basic Arduino loop.  Focuser::loop returns the 
///       amount of time (in micro-seconds) it would like the caller to wait 
///       before invoking Focuser::loop again.
/// - <b> Net Interface: </b>
///       The Net Interface (NetInterface) is where the focuser gets input 
///       and sends output to.  Normally that's the WIFI connection to the 
///       host computer, but there's a Mock Network Interface that's used 
///       for testing.
/// - <b> Hardware Interface: </b>
///       The Hardware Interface (HWI) is how the focuser interacts with
///       the actual hardware.  Normally this as the ESP8266 itself, but
///       there's a Mock Hardware Interface that's used for testing.
/// - <b> Debug Interface: </b>
///       The Debug Interface (DebugInterface) can be used to send debug
///       messages to a host computer.  It's a developer only interface.
/// - <b> Commands: </b>
///       A command is an instruction that comes from the the comes from the 
///       the Net Interface.  i.e., "What is the focuser position",  
///       "Move the focuser to this position".  The list of valid commands 
///       is declared in CommandParser::Command
/// - <b> Invidivual State: </b>
///       The Focuser is most similar to a state machine.  Focuser::loop
///       just runs the handler for the current state. For example, if the
///       current state is "moving to a new position" the focuser might
///       figure out where it is right now, what direction it has to move,
///       and how many steps it needs to take to get to that positon.
/// - <b> State Stack: </b>
///       The Focuser actually has a stack of states.  The stack is useful
///       because it's sometimes easier to describe a complex operation
///       using simpler operations.  i.e., you can move the stepper motor
///       one step by running State::STEPPER_ACTIVE_AND_WAIT and then
///       State::STEPPER_INACTIVE_AND_WAIT.  A move can be done by setting
///       a direction using State::SET_DIR and then using State::DO_STEPS
///       to take multiple steps.
///
namespace FS {

/// @brief Focuser's State Enum
///
/// @see FS Namespace for high level description.
///
enum class State 
{
  START_OF_STATES = 0,        ///< Start of States
  ACCEPT_COMMANDS = 0,        ///< Accepting commands from the net interface
  DO_STEPS,                   ///< Doing n Stepper Motor Steps
  STEPPER_INACTIVE_AND_WAIT,  ///< Set Stepper to Inactive and Pause
  STEPPER_ACTIVE_AND_WAIT,    ///< Set Stepper to Active and Pause
  SET_DIR,                    ///< Set the Direction Pin
  MOVING,                     ///< Move to an absolute position
  STOP_AT_HOME,               ///< Rewind until the Home input is active
  SLEEP,                      ///< Low Power State
  ERROR_STATE,                ///< Error Errror Error
  END_OF_STATES               ///< End of States
};

/// @brief What direction is the focuser going?
enum class Dir {
  FORWARD,    ///< Go Forward
  REVERSE     ///< Go Backward
};

class StateArg
{
  public: 

  enum class Type {
    NONE,
    INT,
    DIR
  };

  StateArg() : type{ Type::NONE}  {}
  StateArg( int i ) : type{Type::INT}, intArg{ i } {}
  StateArg( Dir d ) : type{Type::DIR}, dirArg{ d } {}
  Type getType() { return type; }
  int getInt() { assert( type==Type::INT ); return intArg; }
  Dir getDir() { assert( type==Type::DIR ); return dirArg; }

  private:

  Type type;

  union {
    int intArg;
    Dir dirArg;
  };
};

class TimingParams
{
  public:

  TimingParams( 
    int msEpochBetweenCommandChecksRHS    = 100,        // 100 ms
    int maxStepsBetweenChecksRHS          = 50,
    unsigned msInactivityToSleepRHS       = 5*60*1000,  // 5 minutes
    int msEpochForSleepCommandChecksRHS   = 1*1000,     // 1 seconds
    int msToPowerStepperRHS               = 1*1000,     // 1 second
    unsigned microSecondStepPauseRHS      = 1000        // 1 ms
  ) :
    msEpochBetweenCommandChecks{ msEpochBetweenCommandChecksRHS },
    maxStepsBetweenChecks{ maxStepsBetweenChecksRHS },
    msInactivityToSleep{ msInactivityToSleepRHS },
    msEpochForSleepCommandChecks{ msEpochForSleepCommandChecksRHS },
    msToPowerStepper{ msToPowerStepperRHS},
    microSecondStepPause{ microSecondStepPauseRHS }
  {
  }

  int getEpochBetweenCommandChecks() const 
  { 
    return msEpochBetweenCommandChecks; 
  }
  int getMaxStepsBetweenChecks() const 
  { 
    return maxStepsBetweenChecks; 
  }
  unsigned getInactivityToSleep() const 
  { 
    return msInactivityToSleep; 
  }
  int getEpochForSleepCommandChecks() const 
  { 
    return msEpochForSleepCommandChecks; 
  }
  int getTimeToPowerStepper() const 
  { 
    return msToPowerStepper;
  }
  int getMicroSecondStepPause() const 
  { 
    return microSecondStepPause;
  }

  private:
  int msEpochBetweenCommandChecks;
  int maxStepsBetweenChecks;
  unsigned msInactivityToSleep;
  int msEpochForSleepCommandChecks;
  int msToPowerStepper;
  unsigned microSecondStepPause;
};

enum class Build
{
  LOW_POWER_HYPERSTAR_FOCUSER,
  LOW_POWER_HYPERSTAR_FOCUSER_MICROSTEP,
  TRADITIONAL_FOCUSER,
  UNIT_TEST_BUILD_HYPERSTAR,
  UNIT_TEST_TRADITIONAL_FOCUSER
};


class BuildParams {
  public:

  using BuildParamMap = const std::unordered_map<Build, BuildParams, EnumHash >;

  BuildParams() = delete;

  BuildParams( 
    TimingParams timingParamsRHS,
    bool focuserHasHomeRHS,
    unsigned int maxAbsPosRHS
  ) : 
    timingParams{ timingParamsRHS },
    focuserHasHome{ focuserHasHomeRHS },
    maxAbsPos { maxAbsPosRHS }
  {
  }
  BuildParams( Build buildType )
  {
    *this = builds.at( buildType );
  } 

  TimingParams timingParams;
  bool focuserHasHome;
  unsigned int maxAbsPos;
  static BuildParamMap builds;

  private:
};
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

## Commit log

2018-11-20 - Add the eagle library file for the Wemos IOT board. - Add license and attribution information for the library.
2018-11-20 - Add the sparkfun connectors eagle library that I intend to use in my board design - Add licensing and attribution
2018-11-23 Add eagle libaries under boards Add a sample build under boards
    [beefocus.brd, beefocus.sch]
2018-11-23 Add pictures of the board and schemantic
2018-11-25 - Rename the ino file for the focuser so it will compile with the arduino SDC. - Move wifi ssid and password into a separate file - Update the README.md and add a TODO.md
2018-11-25 - Firmware change to test sleep mode on the stepper motor controller. - Keeping a stepper motor active draws a lot of current, and for a lot of focuser solutions the focuser won't move if you power d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
    [focuser_state.cpp, focuser_state.h]
2018-11-27 - Added prototype, untested gerber files for the nema 14 board. - Updated TODO. The plan is to migrate the TODO items onto the git hub issue tracker.
    [copper_bottom.gbr, drills.xln, profile.gbr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]
2018-11-28 Convert gerber files to RS-274-X format for compatibility with PCB FAB
    [copper_bottom.gbr, drills.xln, profile.gbr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]
2018-12-01 Create a script to download the Arduino SDK
2018-12-04 Update README.md to add links to current content.
2018-12-07 Add a script to install gtest Modify .travis.yml to allow sudo (for gtest install) and install gtest Rename build script to build-all.sh Open the process_int interface so it can be tested Create a pr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
2018-12-08 Change HardwareInterface class to HWI
    This is a code readability change.
    Before: The step once pin was HardwareInterface::Pin::STEP
    After The step once pin is HWI::Pin::STEP
2018-12-09 Cleanly separate the command parser + unit testing
    - Move status out of the command parser
    - Remove 'deltas' and replace with a 'command packet'
    - Update focuser_state.cpp
    - Add some simple mocks for unit testing
    - Unit test command parser cases
    - Change the simulator so it prints network activity instead of debug logs.
    [focuser_state.cpp, main.cpp]
2018-12-14 Use an ENUM type for the pin mode.
2018-12-16 Add ABS_POS test to the unit tests Clean up focuser state a bit so it doesn't do as may state transitions
    [focuser_state.cpp, focuser_state.h, test_focuser_state.cpp]
2018-12-16 Filter non-functional debug lines from the unit test output Don't call setup on focuser state in actual arduino code
2018-12-16 Clean up focuser command processing
    - Remove error state from focuser state. It's too hard to reason about.
    - Refactor state_accept_commands so it doesn't always pause 10 seconds after getting a command
    - Reflect the change to state_accept_commands in the focuser_state unit test
    - Separate, more cleanly, the getting of a command from the processing of the command.
    [focuser_state.cpp, focuser_state.h, test_focuser_state.cpp]
2018-12-16 Fix some logic errors exposed in unit testing.
    - Change stepper states to active and inactive, for clarity
    - Stepper now switches from inactive to active and back to do 1 step
    - There is now a 1ms pause when we switch directions
    - Unit tested double forward abs and blacklash rewind the forward.
    [focuser_state.cpp, focuser_state.h, hardware_interface.h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]
2018-12-17 Add Interruptable Flag to Focuser State. All steps are now 1ms
    - Add a "will this command interrupt" flag to the focuser state
    - Make all steps 1ms. It's close to what we already do and saner for testing
    - Move the enum advance into basic_types.h
    - Some other clean-ups
2018-12-18 Focuser State switch to map
    - Redo the focuser state switch as an unordered map
    - Add a unit test to make sure all states have implementations
2018-12-19 Interface Cleanup and Unit Testing Documentation
    - Removed the reset from the net interface
    - Removed the extra simple net interfaces. Everything can be done using
    the timed interface
    - Documented events and cleaned up some of the interface for events.
    [main.cpp, test_focuser_state.cpp]
2018-12-21 Documment the net interface mock & clean-up
    - Document the net interface mock
    - Remove the comment filter from the net interface mock - it's not core
    functionality
    - Put includes in alphabetical order
2018-12-21 Fix Arduino warnings
2018-12-22 Remove sleep and wake commands for simplification. Test interruptions.
    - Remove sleep and wake. The caller shouldn't have to set this state.
    - Fix and test move interrupions.
    [focuser_state.cpp, focuser_state.h, test_focuser_state.cpp]
2018-12-22 More interrupt while blank implementation and testing.
2018-12-22 Tests for home interruptions and implementation.
2018-12-22 Fix bug in backlash correction interrupts. Refactor focuser stack. Warnings.
    - Fixed a bug in the backlash correction interrupt code.
    - Test backlash correction interrupts
    - Refactored the focuser stack to hide vector implementation.
    - Fix warnings
    [focuser_state.cpp, focuser_state.h, test_focuser_state.cpp]
2018-12-23 Bug fixes from board testing
    - Use Delay() where possible. I suspect DelayMicroseconds doesn't service the Wifi
    - Turn off writing the wifi configuration to flash
    - Add a maximum stack-size guard to the focuser state-stack.
    [focuser_state.h, main.cpp]
2018-12-23 Board Power Testing + Fix Home Bug
    [focuser_state.cpp, focuser_state.h, test_focuser_state.cpp]
2019-01-05 Update board to fix lost trace to ground :(
    [beefocus.brd, beefocus.sch]
2019-01-05 Name fixing in code and comments.
    [focuser_state.cpp, focuser_state.h, test_focuser_state.cpp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]
2019-02-02 Opps, wrong max position for my build
    [focuser_state.cpp, test_focuser_state.cpp]
2019-03-03 Add button number examples
2019-03-18 Update readme with current status
2019-03-26 Fix javascript for SSID text button - now displays text content.
2019-03-31 Update board to take a push button switch. This will be used to do a hard reset in the future
    [beefocus.brd, beefocus.sch]
2019-04-13 Change microstepping to 1/16th on board.
    [beefocus.brd, beefocus.sch]
2019-04-13 Revised gerber files
    [copper_bottom.gbr, drills.xln, silkscreen_top.gbr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]
2019-05-03 Clang build + clang warnings fixes (including one functional bug in the Unit Tests).
    [hardware_interface.h, main.cpp]
2019-05-26 Start another circuit board variant.
    [beefocus.brd, beefocus.sch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]
2019-05-31 Modifications so the gerber files are acceptable to allpcb.com
    [copper_bottom.gbr, drills.xln, profile.gbr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]
2019-06-22 Add command to shut down debug output. Create a new board profile for micro-stepping boards.
2019-06-23 Fix timeouts while writing IO
    - Add the concept of a flush to the output streams
    - Buffer output until flush (or the buffer becomes full)
    - Set no delay writes
    - Turn off wifi power saving mode until the write buffer is clear
    [focuser_state.cpp, main.cpp]
